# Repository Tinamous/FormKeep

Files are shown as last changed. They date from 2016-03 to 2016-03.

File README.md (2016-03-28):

Form Keep
=========

A UV exposure box and Tray store (to keep your trays in) for the Form 1, 1+ and 2 printers.

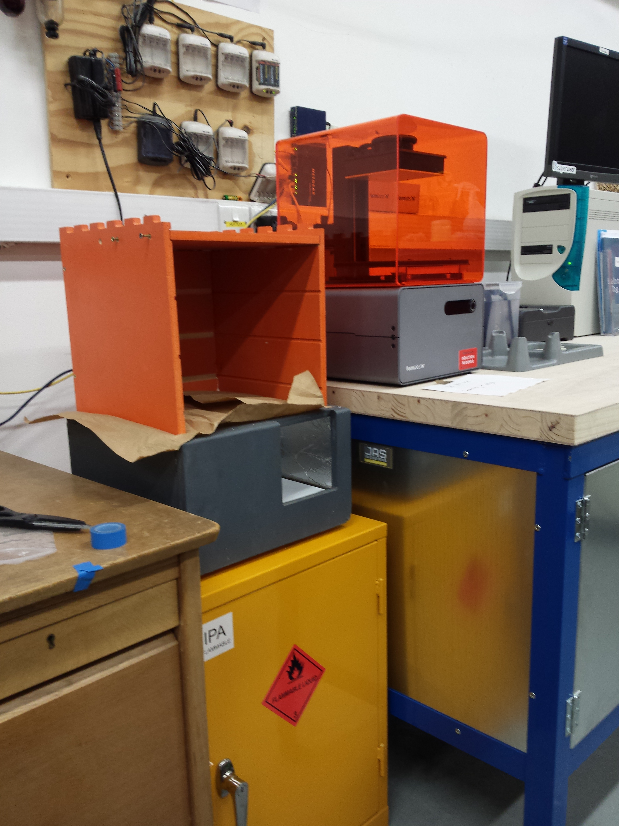
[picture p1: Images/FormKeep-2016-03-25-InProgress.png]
Form Keep UV box and tray storage


Features:
* UV exposure in base unit on 30 minute timer with countdown "clock" style neopixel display on front door.
* 3x shelfs for tray storage.
* 1x top open shelf for sand paper storage
* 1x small (25mm) area under lowest shelf for possible other storage
* Door sensors for top unit to tell if the door is open, and hence light getting to trays
* Ventilation in the base unit to prevent a build up of IPA vapours in the box
* White LEDs in base unit to allow the part to be seen clearly when the door is open

Construction:
* Top and bottom units are made of 12mm MDF (2 sheets 600x1200mm)
* Door on base made from 18mm MDF
* Feet made from 12mm MDF glued to base, then adjustable feet set into that
* Door for top unit made with 3mm acrylic
* Shelfs made with 5mm acrylic, colour to match the resin
* Front door panel 3mm clear acrylic
** 3D printed support for 12 pixel NeoPixel ring for count down timer
* Fan panel made with 3mm acrylic (ideally a scrap piece as it's not seen)
* Fan is 80mm PC fan (with yellow pulse wire ignored)
* Base panel 3mm acrylic. Can be any color
* Inside is coated with tin foil (glued to the MDF) to help reflect the UV rays

Cut using CNC router, can be hand cut if no CNC available using the svg files as cutting plans.

Roundovers done by hand router as it's quicker. 
* Bottom of the base unit has large round over on each side coming out thought the door but not along door.
* Top of base unit has small round over on sides and front of door.

Painting:
* Base unit grey (The grey in the picture is actually just undercoat which works well).
* Top unit orange

Electronics:
* Uses V2.00 Kitchen Lights Controller from https://github.com/Tinamous/KitchenLightsController
* Channel 1 & 2 used to drive UV LEDs. 
* 2x 5M strips of UV LEDs, split into 900mm lengths (to make it easier to fit), each individually wired back to the PCB.
* 2x 300mm White LEDs connected to channel 3
* 1x PC fan connected to channel 4 with protection diode across either the terminal block or headers (depending on which is free).
* USB power controller not fitted to board.
* Max 0.05R current sense resistor (5-10A load due to UV LEDs).
* Hall effect transistor used for door sensor (rather than have switch in possible explosive environment of IPA vapours).
** Connected to Button input on PCB
* Hall effect sensor to top unit door on PIR input
* TEMT6000 breakout board for light level sensor on top unit connected to Light Sensor on PCB
* Optional temperature sensors in base and top units connected to temperature sensor input
* Optional buzzer wired on breakout area of PCB.
* 12 pixel NeoPixel ring. 12th (last) pixel should be at 12 O'Clock position
** https://www.adafruit.com/products/1643
* Use 5V switching regulator rather than 7805 due to NeoPixel load (see eBay), or fit good heatsink to 7805. (360mA max load from NeoPixels, + 100mA from Photon).
* Needs a good 5-10A 12V DC power supply.
* Use Particle Photon to drive, connect to Tinamous.com to allow remote monitoring of light, temperature and more inportantly time remaining.

Bugs
----

* Back Panel slots are out of alignment with side panel slots on top unit.
* Top unit slots are to shallow (3mm, with 1mm error on Z alignment due to MDF varience and 1mm allowance for tollerance on the acrylic shelfs this leaves a potential 1mm overlap on one side.
* Front foor, opening is far to big (much bigger than Form2 display).
* Ribon cable pocket is not deep enough on base.
* Top shelf currently split in 2 which is not ideal for stopping the light get into the top resin tray. Needs an extra sheet.

Timing: See http://formlabs.com/support/finishing/post-curing-prints/

[MainPicture]: https://github.com/Tinamous/FormKeep/raw/master/Images/FormKeep-2016-03-25-InProgress.png "Form Keep UV box and tray storage - In Progress"

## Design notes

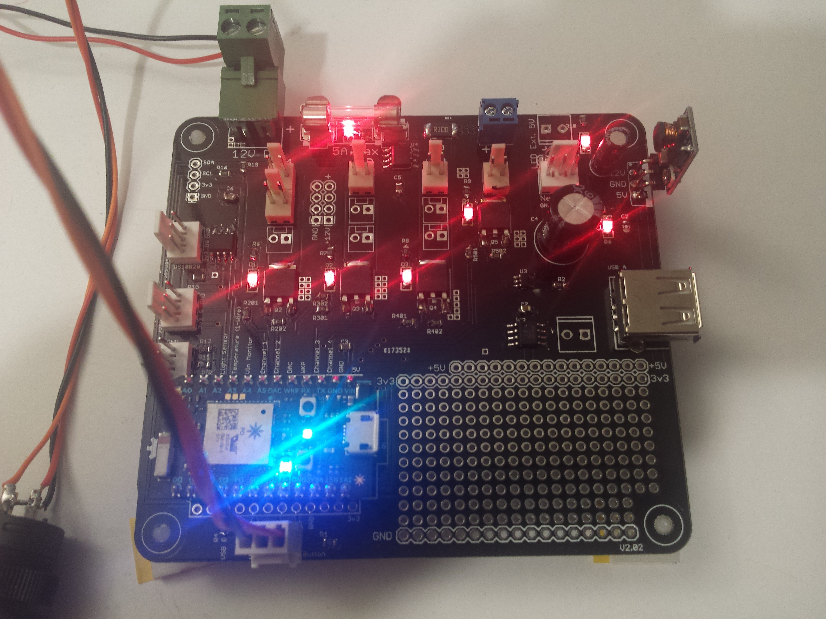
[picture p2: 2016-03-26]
Images/FormKeep-2016-03-20-PCB.png

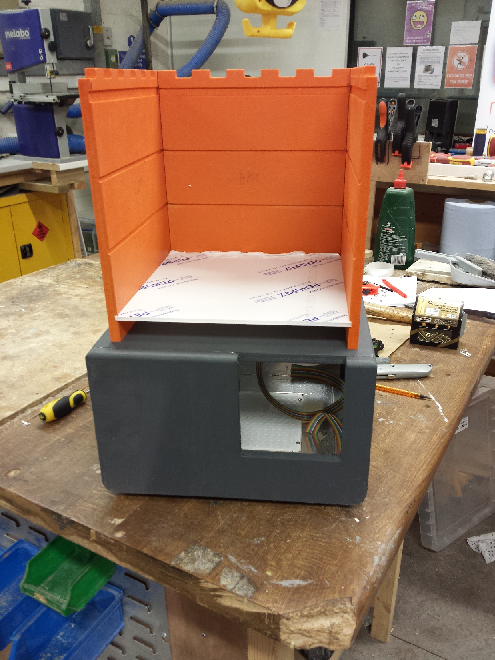
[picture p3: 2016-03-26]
Images/FormKeep-2016-03-25-WithShelf.png

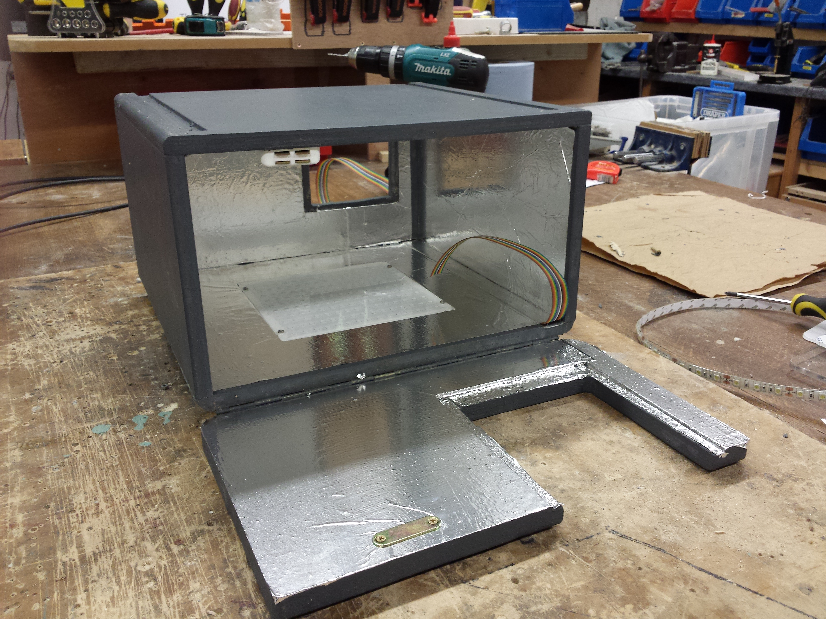
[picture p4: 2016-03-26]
Images/FormKeep-2016-03-25-InsideBase.png

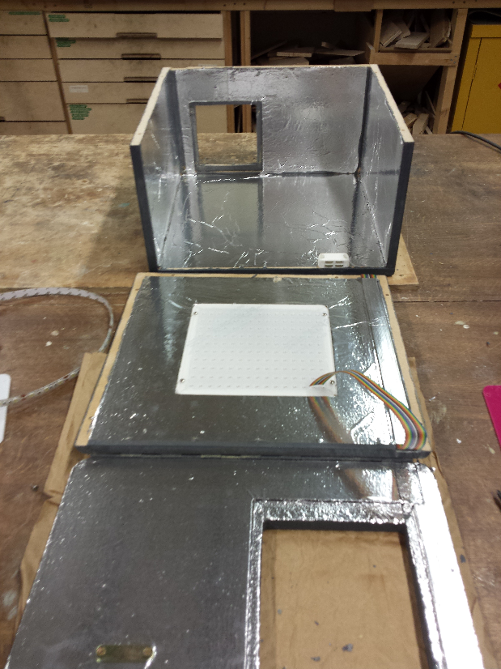
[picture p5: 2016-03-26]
Images/FormKeep-2016-03-25-InsideBaseOpen.png

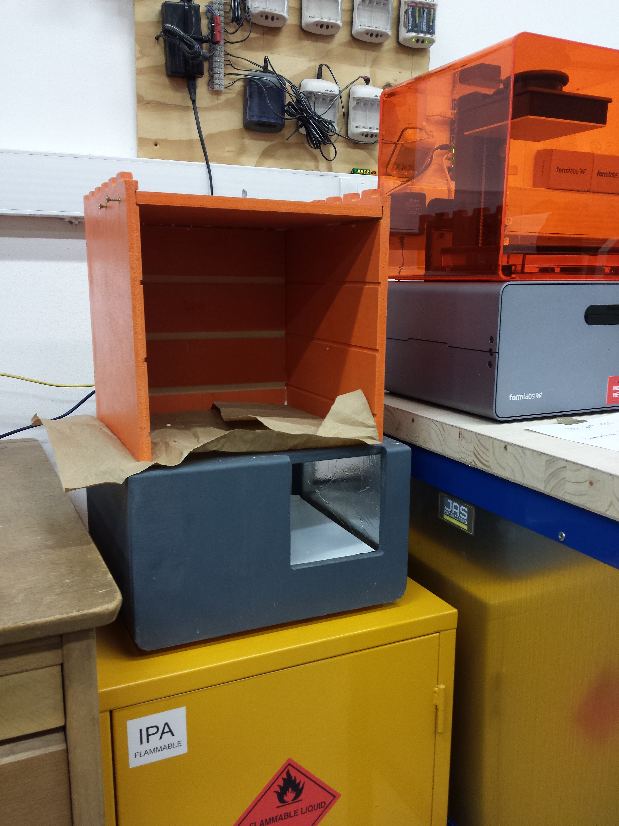
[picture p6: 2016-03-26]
Images/FormKeep-2016-03-25-InProgress-2.png

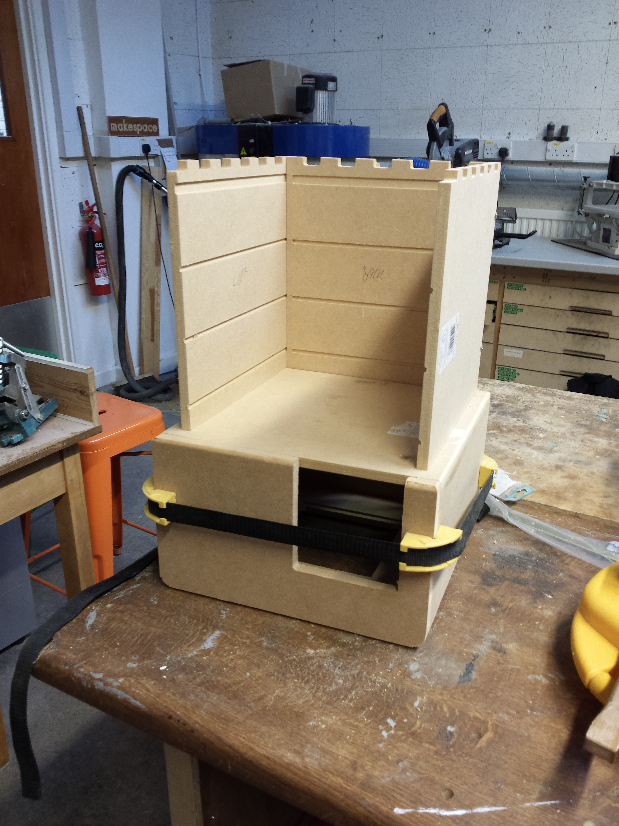
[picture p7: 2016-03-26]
Images/FormKeep-2016-03-22-BeforePaint.png

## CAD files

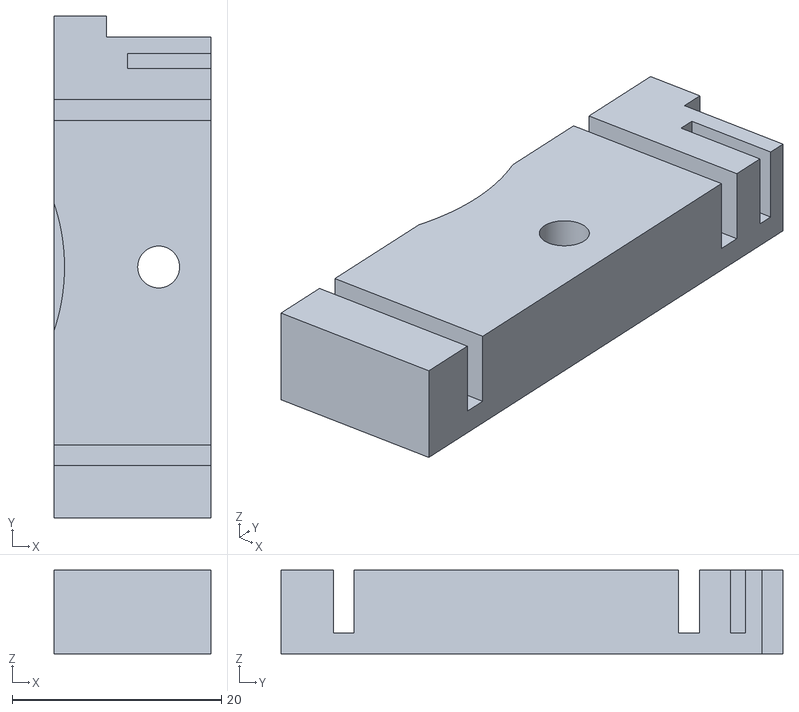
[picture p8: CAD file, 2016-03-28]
3D Printed/FrontPanelSupport.stl
15.0 x 48.0 x 8.00

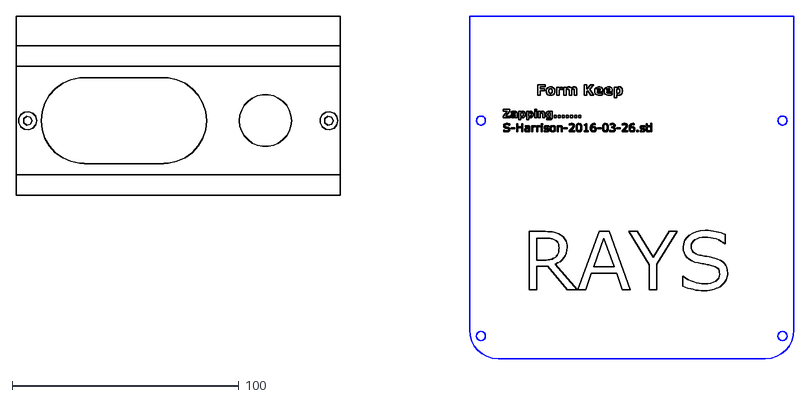
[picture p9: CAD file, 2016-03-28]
Acrylic/FormKeep-FrontPanel-Acrylic-3mm-Clear-With3DPrintedThing.dxf
343.0 x 151.0

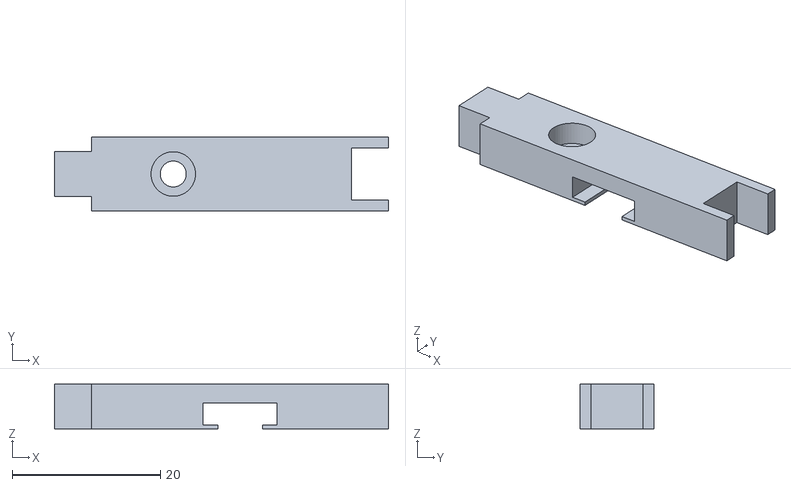
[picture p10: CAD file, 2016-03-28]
3D Printed/LedStripHolder-Single.stl
45.0 x 10.0 x 6.00

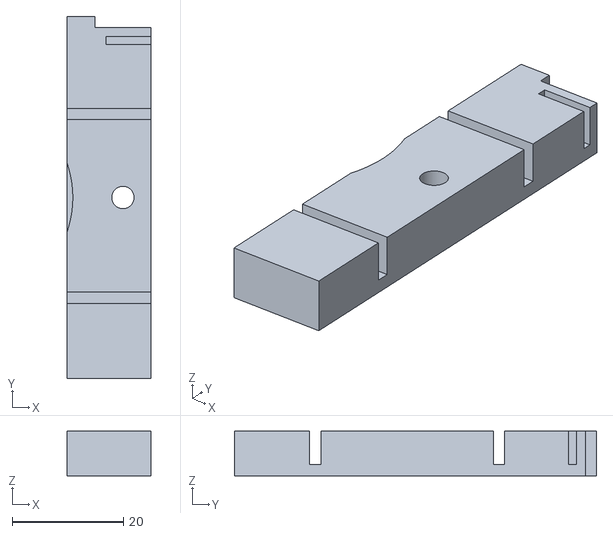
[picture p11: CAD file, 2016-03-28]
3D Printed/FrontPanelSupport-High.stl
15.0 x 65.0 x 8.00

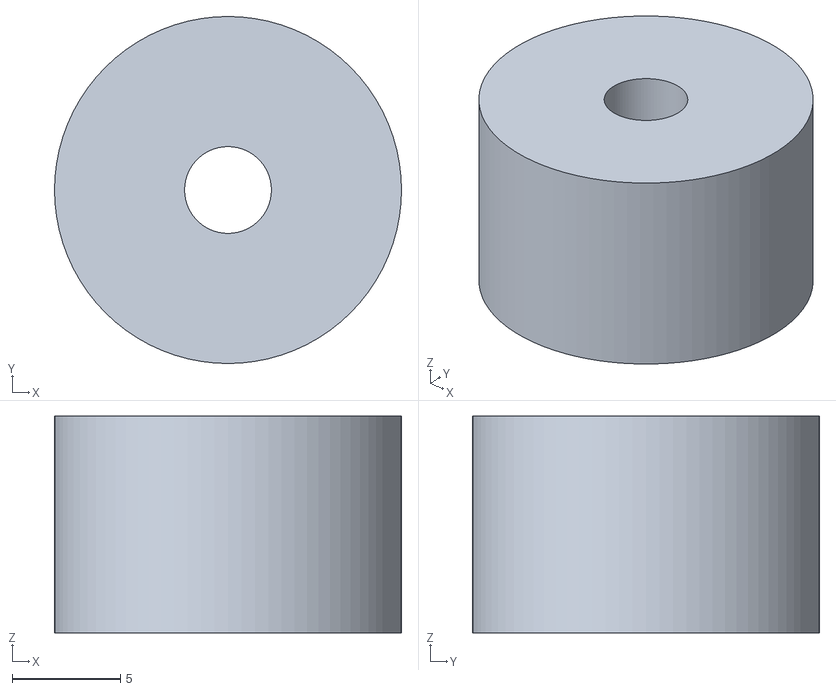
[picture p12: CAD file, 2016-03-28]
3D Printed/PcbStandoffs.stl
16.0 x 16.0 x 10.0

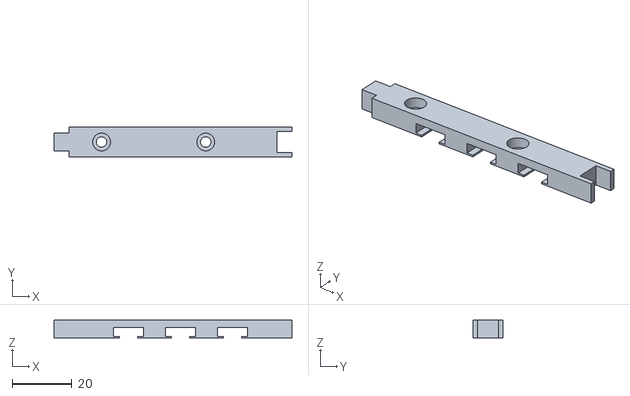
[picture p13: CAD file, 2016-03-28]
3D Printed/LedStripHolder-DoubleWidth-TrippleHolder.stl
80.0 x 10.0 x 6.00

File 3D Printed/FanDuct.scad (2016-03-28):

width = 80;
distanceBetweenHoles = 72; //
fanDuctDiameter = 74;
$fn = 128;

holeOffset = (width-distanceBetweenHoles) / 2;

module basePlate() {
    difference() {
        union() {
            cube([width,width,2]);
        }
        union() {
            translate([width/2, width/2,0]) {
                cylinder(d=fanDuctDiameter, h=2);
            }
        }
    }
}

module fanScrewHoles() {
    translate([holeOffset,holeOffset,0]) {
        cylinder(d=4, h=3);
    }

    translate([width -holeOffset,holeOffset,0]) {
        cylinder(d=4, h=3);
    }

    translate([holeOffset,width-holeOffset,0]) {
        cylinder(d=4, h=3);
    }

    translate([width -holeOffset, width - holeOffset,0]) {
        cylinder(d=4, h=3);
    }
}

ductHeight = 100;
ductDepth = 50;

module hollowCube() {
    translate([0,0,5]) {
        rotate([12,0,0]) {
            difference() {
                union() {
                    translate([(width-fanDuctDiameter+8)/2, 6, 0]) {
                        cube([fanDuctDiameter-8, ductHeight, ductDepth]);
                    }
                }
                union() {
                    translate([(width-fanDuctDiameter+8)/2+4, 6+4, 0]) {
                        cube([fanDuctDiameter-8-8, ductHeight+8, ductDepth-2]);
                    }
                }
            }
        }
    }
}


difference() {
    union() {
        basePlate();
        // Hull section between basePlate and hollow cube.
        hollowCube();
    }
    union() {
        fanScrewHoles();
    }
}

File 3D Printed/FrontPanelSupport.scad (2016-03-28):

$fn = 200;

// Ideal panel width was 115mm
// but cut was outside marking
// so is actually 143mm wide with 9mm overlap.
// If you cut yours correctly reduce this.
// Excludes possible fixing to wooden door.
PanelWidth = 143; // mm Actylic panel only. 

// Offset from left/right side for the mounting holes on the panel
MountingHolesOffset = 5;

// Height of the Acrylic panel
// need to exclude top 12-15mm for unit overlap. 
// Botton has rounded corners.
PanelHeight = 151; // mm

NeoPixelRingOuterDiameter = 38; // mm
NeoPixelRingInnerDiameter = 23; // mm

Height = NeoPixelRingOuterDiameter + 10 + 17; // 5mm top/bottom.
Depth = 8; // mm

NeoPixelXPosition = 110; 
NeoPixelYPosition = Height / 2; //24mm from the top. // Height / 2;
NeoPixelHeight = 4.5; // mm - includes wires (& probably hotmelt)

module frontPanelInsert() {
    difference() {
        union() {
            cube([PanelWidth, Height, Depth]);
        }
        union() {
            // Mounting holes
            translate([MountingHolesOffset, Height/2, 0]) {
                cylinder(d=4, h=Depth, centre=true);
                cylinder(d=8, h=3, centre=true);
            }
            translate([PanelWidth-MountingHolesOffset, Height/2, 0]) {
                cylinder(d=4, h=Depth, centre=true);
                cylinder(d=8, h=3, centre=true);
            }
           
            
            // Hole through the block for light to come through the center of the NeoPixel Display
            translate([NeoPixelXPosition, NeoPixelYPosition, 0]) {
                cylinder(d=NeoPixelRingInnerDiameter, h=Depth, centre=true);
                
                translate([0,0, Depth-NeoPixelHeight]) {
                    cylinder(d=NeoPixelRingOuterDiameter, h=NeoPixelHeight, centre=true);
                }
            }
            
            // Pocket for NeoPixel ring to sit in.
            
            // Channels for wires to escape from NeoPixels.
            // 2mm from top, exit to the right of the neo pixels
            translate([NeoPixelXPosition, NeoPixelYPosition + (NeoPixelRingOuterDiameter/2)-2-3, 2]) { 
                // Din/DOut wires.
                cube([PanelWidth - NeoPixelXPosition, 2, Depth-2]);
            }
            
            translate([NeoPixelXPosition, NeoPixelYPosition - (NeoPixelRingOuterDiameter/2), 2]) { 
                // +Ve and GND
                cube([PanelWidth - NeoPixelXPosition, 2, Depth-2]);
            }
            
            // Oval cutout to look like Form1.
            translate([30, NeoPixelYPosition, 0]) {
                cylinder(d=NeoPixelRingOuterDiameter, h=Depth, centre=true);
                
                translate([0,-(NeoPixelRingOuterDiameter/2), 0]) {
                    cube([35 ,NeoPixelRingOuterDiameter,Depth]);
                }
                
                translate([35,0, 0]) {
                    cylinder(d=NeoPixelRingOuterDiameter, h=Depth, centre=true);
                }
            }
            
            // cut out for Hall Effect door sensor.
            magnetHeightAllowance = 2; // mm
            translate([PanelWidth-10, Height-magnetHeightAllowance, 0]) {
                // Cut out all the way trough to allow for the magnet offset from 
                // the lid of the unit.
                #cube([10, magnetHeightAllowance, 10]);
                
                // Make a pocket for the hall effect device.
                // Move in slightly to allow for x-axis error on magnet alignment.
                // Move down slightly to allow for a wall on the panel
                // Move up down so as to not cut all the way through the panel.
                // and mount it at the back of the panel
                translate([2, -3, 2]) {
                    // Hall effect is about 1.6mm deep
                    #cube([10, 1.5, Depth-2]);
                }
            }
            
            // DEGUB!
            // Chop out most of the panel to get just the hall effect section
            // in order to test print
            cube([PanelWidth-15, Height, Depth]);
        }
    }
}

frontPanelInsert();

// For SVG explort

projection( cut=false ) {
//    frontPanelInsert();
}

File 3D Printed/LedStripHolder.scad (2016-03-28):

// Max height 270mm.
// Make 200mm height so 70mm bottom of box for raised
// area that will allow solvent to drain from part.
MaxHeight = 250;
MaxHeight = 70;
//MaxHeight = 35;

blockSize = 35; // 35mm (excludes key slot).

blockKeyWidth = 6;

blockDepth = 6;

// 1 == Single
// 2 == Double with middle strip.
blockType = 2;

$fn=50;

module ledGrip() {
    
                
    // LED strip holes
    translate([0,0,0.5]) {
        cube([10,10,3]);
    }

    // 2mm offset either side to keep hold of the LED.
    translate([2,0,0]) {
        cube([6,10,0.5]);
    }
}

// If multiple blocks use zero tollerance
// includeMiddleStripHolder - if holder for LED strip in the middle of the two main ones.
// i.e. for white LED strip between the two UV strips.
module block(blockCount, blockConnectTollerance, includeMiddleStripHolder) {

length = (blockCount * blockSize) + 5 ;

    difference() {
        union() {
            translate([0,2,0]) {
                cube ([length,blockKeyWidth,blockDepth]);
            }
            
            // Move down 10mm
            // Add outer blocks either side
            // to connect one segment to the next.
            translate([5,8,0]) {
                cube([length,2,blockDepth]);
            }
            
            translate([5,0,0]) {
                cube([length,2,blockDepth]);
            }
        }
        union() {
            
            for (offset = [16 : 35 : length]) {
            
                // Mounting holes
                translate([offset,5,0]) {
                    cylinder(d=3.5,h=blockDepth);
                    
                    // Large hole for head of screw
                    translate([0,0,3]) { 
                        cylinder(d=6,h=blockDepth-3);
                    }
                    
                }
            }
            
            // Holes to hold the LED strip in place.
            for (offset = [20 : 35 : length-10]) {
                translate([offset,0,0.0]) {
                    ledGrip();
                }
            }
            
            // for double strips, insert a middle
            //  
            if (includeMiddleStripHolder) {
                for (offset = [37.5 : 70 : length]) {
                    translate([offset,0,0.0]) {
                        ledGrip();
                    }
                }
            }
            
            // cut out a tiny bit extra from the open end to 
            // allow for variance in printing
            // Offset is 2mm either wide.
            translate([length,2 - blockConnectTollerance,0]) {
                // Allow 0.5mm spacing for key to fit.
                cube ([5,blockKeyWidth + (2* blockConnectTollerance),blockDepth]);
            }
        }
    }
}

//block(2, 0.5, true);
//block(2, 0.5, false);

if (blockType == 1) {
    block(1, 0.5, false);
} else if (blockType == 2) {
    block(2, 0.5, true);
}

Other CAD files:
3D Printed/PcbStandoffs.scad

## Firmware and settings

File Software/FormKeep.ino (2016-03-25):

// This #include statement was automatically added by the Particle IDE.
#include "IdleState.h"

// This #include statement was automatically added by the Particle IDE.
#include "TimerRunningState.h"

// This #include statement was automatically added by the Particle IDE.
#include "adafruit-ina219/adafruit-ina219.h"

// This #include statement was automatically added by the Particle IDE.
#include "neopixel/neopixel.h"

// This #include statement was automatically added by the Particle IDE.
#include "OneWire/OneWire.h"

//////////////////////////////////////////////////////////////////////////
// FORM [1/1+/2] KEEP. UV box control + monitoring.
//////////////////////////////////////////////////////////////////////////
// V2.02  board
//////////////////////////////////////////////////////////////////////////
int BoardVersion = 3;

// D0/D1 - I2C only

// USV String 1
int uvString1Pin = A4; // Channel 1
int uvString2Pin = A5; // Channel 2
int whiteLedsPin = RX; // Channel 3
int fanPin = TX; // Channel 4

// User panel switch
// Door sensor hall effect switch input
int switchPin = D6;
// Door sensor hall effect Power.
int switchDrivePin = D7;

int vInPin = A3;
OneWire ds = OneWire(A2);  // 1-wire signal on pin D4
int lightLevelPin = A1;
int pirPin = A0;



// byte sensor1[] = {0x28, 0xD6, 0xA9, 0x4E, 0x07, 0x00, 0x00, 0x27};
// onboard temperature sensor address.
// TODO: Allow for UV box temperature, Upper box temperature and external temperature.
byte sensor[8];

// Current sensor
Adafruit_INA219 ina219;

//////////////////////////////////////////////////////////////////////////
// Particle Functions
//////////////////////////////////////////////////////////////////////////
int on(String command);
int off(String command);
int startTimer(String command);
int stopTimer(String args);
int setTimer(String args);

//////////////////////////////////////////////////////////////////////////
// State
//////////////////////////////////////////////////////////////////////////
// State:
// 0: Idel
// 1: timer running
// 10: timer complete, waiting for user to remove the itme
int currentState = 0;

//////////////////////////////////////////////////////////////////////////
// Interrup flags
//////////////////////////////////////////////////////////////////////////
volatile bool doorOpened = false;
volatile bool trayDoorOpened = false;


// Setup NeoPixel (clock) circle.
#define PIXEL_PIN D5
#define PIXEL_COUNT 12
#define PIXEL_TYPE WS2812B

Adafruit_NeoPixel strip = Adafruit_NeoPixel(PIXEL_COUNT, PIXEL_PIN, PIXEL_TYPE);

// Monitoring variables
float temperatureCelsius = 0;
double currentMilliAmps = 0;
double voltsIn = 0; // 5V rail monitor.
double supplyVoltage = 0; // the 12V in (monitored via current sensor)

// How many seconds to wait before turning off the lights.
double lightsOffInSeconds = 0;

// Measurement timer. Every n seconds.
Timer countDownTimer(1000, countDownTimerTick);

void setup() {
    
    // Setup NeoPixel LED (strip).
    strip.begin();
    strip.show(); // Initialize all pixels to 'off'
    
    // Smile.
    for (int i=2; i<=8; i++ ) {
        strip.setColorDimmed(i, 0, 255, 0, 128);
    }
    strip.setColorDimmed(0, 0, 0, 255, 128);
    strip.setColorDimmed(10, 0, 0, 255, 128);
    strip.show();
    
    // Power drives.
    pinMode(uvString1Pin, OUTPUT);
    pinMode(uvString2Pin, OUTPUT);
    pinMode(whiteLedsPin, OUTPUT);
    pinMode(fanPin, OUTPUT);
    
    // Switch
    pinMode(switchPin, INPUT_PULLUP); // Interrupt.
    pinMode(switchDrivePin, OUTPUT);
    
    // Sensors
    pinMode(vInPin, INPUT);
    pinMode(lightLevelPin, INPUT);
    // PIR input must be reduced to guard against 5v.
    pinMode(pirPin, INPUT); // Hall effect #2 on upper case
    
     
    digitalWrite(uvString1Pin, false);
    digitalWrite(uvString2Pin, false);
    digitalWrite(whiteLedsPin, false);
    digitalWrite(fanPin, false);
    digitalWrite(switchDrivePin, true);
     
    Particle.function("startTimer", startTimer);
    Particle.function("stopTimer", stopTimer);
    Particle.function("on", on); // Args: "Fan", "UV", "White"
    Particle.function("off", off);// Args: "Fan", "UV", "White"
    Particle.function("setTimer", setTimer); // Args: time in seconds for the standard timer.
    
    // Initialize the INA219.
    // By default the initialization will use the largest range (32V, 2A).  However
    // you can call a setCalibration function to change this range (see comments).
    // NB: Check which resistor is to be used. Probably 0R05 due to high current.
    ina219.begin();

    // interrupt on the falling edge of A7 (switch pulled low)
    attachInterrupt(switchPin, doorOpenedIsr, FALLING);
    
    // attachInterrup to PIR (Hall effect #2) pin
    attachInterrupt(pirPin, upperDoorOpenedIsr, RISING);
    
    listTemperatureSensors();

    Particle.publish("Status", "Form Keep. Version: 0.2.1.");
    Particle.publish("Version", "0.2.1");
    
    
    //countDownTimer.start();
}

int loopCounter = 0;
// the last value of lightsOffInSeconds that was used for setting the clock.
int lastLightsOffInSeconds = 0;
bool doorOpen = false;
bool trayDoorOpen = false;
bool uvLedsOn = false;
bool whiteLedsOn = false;
bool fanOn = false;

void loop() {
    if (currentState == 1 && lightsOffInSeconds <=0) {
        stopUVTimer();
    }
    
    loopCounter++;
    if (loopCounter > 200) {
        loopCounter = 0;
        //takeMeasurements();
    }
    
    if (doorOpened) {
        Particle.publish("Status", "Door opened.", 60, PRIVATE);
        
        // If currently idle waiting for blah...
        if (currentState == 0) {
            // Immediatly start the fan to keep IPA vapours low
            switchFanOn();
            switchWhiteLedsOn();
            waitForDoorClose();
            startUVTimer();
        }
        
        // If currently running UV Timer
        if (currentState == 1) {
            // leave lights on.
            // Don't switch the lights on when opened during UV exposure.
            // switchWhiteLedsOn();
        }
        
        // Finished waiting for user to open door.
        if (currentState == 10) {
            Particle.publish("Status", "State = 10, moving to state 0", 60, PRIVATE);
            // user is taking thing out.
            waitForDoorClose();
            switchWhiteLedsOff();
            // restore state to idle.
            currentState = 0;
        }
        
        // Debouce.
        delay(500);
        doorOpened = false;
    }
    
    // if the tray door was opened and it is not already open
    if (trayDoorOpened) {
        Particle.publish("Status", "Tray door opened.", 60, PRIVATE);
        trayDoorOpen = true;
        trayDoorOpened = false;
    }
    
    if (trayDoorOpen) {
        // Check to see if it has now been closed.
        // if so, we can set trayDoorOpen to false.
        // If it's been open for some time we
        // need to beep......
    }
    
    if (lightsOffInSeconds != lastLightsOffInSeconds ) {
        lastLightsOffInSeconds = lightsOffInSeconds;
        
        // Update Neopixel clock.
        for (int i=0; i<12; i++) {
            // uint16_t aLedNumber, byte aRed, byte aGreen, byte aBlue, byte aBrightness
            if (lightsOffInSeconds > ((11-i) * 10)) { // each pixel worth 10 seconds
                strip.setColorDimmed(i, 0, 255, 255, 128);
            } else {
                strip.setColorDimmed(i, 0, 0, 0, 0);
            }
        }
        strip.show();
    }
    
    if (!isDoorClosed()) {
        switchWhiteLedsOn();
    }
    
    if (whiteLedsOn && isDoorClosed()) {
        // Ensure the White LED is switched off if the door was opened but
        // is now closed.
        switchWhiteLedsOff();
    }
    
    updateFanSpeed(!isDoorClosed());
    
    delay(50);
}

void waitForDoorClose() {
    // TODO: Read switch input until or high...

    // switchPin is LOW when door is open.
    while (!digitalRead(switchPin)) {
        delay(10);
    }
    //Particle.publish("Status", "Door closed.", 60, PRIVATE);
}

// Timer.
void countDownTimerTick() {
    lightsOffInSeconds--;   
}

void startUVTimer() {
    // TODO: Use EEPROM value
    lightsOffInSeconds = 120;
    
    switchUVOn();
    switchWhiteLedsOff();
    switchFanOn();
    currentState = 1;
    
    // Update Neopixel clock to show full time
    for (int i=0; i<12; i++) {
        strip.setColorDimmed(i, 0, 255, 0, 128);
    } 
    strip.show();
            
    countDownTimer.start();
    
    Particle.publish("Status", "Timer Started", 60, PRIVATE);
}

void stopUVTimer() {
    countDownTimer.stop();
    
    // UV Exposure finished. Now waiting for user to open door to 
    // remove their thing.
    currentState = 10;
    
    switchUVOff();
    switchFanOff();
    
    for (int i=0; i<12; i++) {
        strip.setColorDimmed(i, 0, 0, 0, 0);
    }
    strip.show();
    
    // TODO: Use EEPROM value
    if (lightsOffInSeconds = 0) {
        Particle.publish("Status", "UV Exposure Complete.", 60, PRIVATE);
    } else {
        Particle.publish("Status", "Timer Stopped", 60, PRIVATE);
    }
}

void switchUVOn() {
    if (uvLedsOn) {
        return;
    }
    Particle.publish("Status", "UV On", 60, PRIVATE);
    digitalWrite(uvString1Pin, true);
    digitalWrite(uvString2Pin, true);
    uvLedsOn = true;
}

void switchUVOff() {
    if (!uvLedsOn) {
        return;
    }
    Particle.publish("Status", "UV Off", 60, PRIVATE);
    digitalWrite(uvString1Pin, false);
    digitalWrite(uvString2Pin, false);
    uvLedsOn = false;
}

void switchWhiteLedsOn() {
    if (whiteLedsOn) {
        return;
    }
    digitalWrite(whiteLedsPin, true);
    whiteLedsOn = true;
    Particle.publish("Status", "White LEDs On", 60, PRIVATE);
}

void switchWhiteLedsOff() {
    if (!whiteLedsOn) {
        return;
    }
    digitalWrite(whiteLedsPin, false);
    whiteLedsOn = false;
    Particle.publish("Status", "White LEDs Off", 60, PRIVATE);
}

void updateFanSpeed(bool doorOpen) {
    // If the door is open, fan runs 100%.
    
    // If running 
        
    if (doorOpen) {
        if (!fanOn) {
            switchFanOn();
        }
        analogWrite(fanPin, 255, 25000);
        return;
    } 
    
    // If not currently in the timer then switch the fan off when the door is closed.
    if (currentState!=1) {
        //switchFanOff();
        return;
    } 
    
    // If within the first x of the timer, keep the fan running low.
            
    // After a preset time the vapoures should have gone
    // so we can kill the fan.
    if (lightsOffInSeconds < 10) { // 90
        switchFanOff();
        return;
    }
    
    // Otherwise run the fan slowly
    analogWrite(fanPin, 80, 25000);

}

void switchFanOn() {
    if (fanOn) {
        return;
    }
    Particle.publish("Status", "Fan On", 60, PRIVATE);
    
    // Start it fast to ensure it starts.
    analogWrite(fanPin, 255);

    //digitalWrite(fanPin, true);
    fanOn = true;
}

void switchFanOff() {
    if (!fanOn) {
        return;
    }
    Particle.publish("Status", "Fan Off", 60, PRIVATE);
    digitalWrite(fanPin, false);
    fanOn = false;
}

bool isDoorClosed() {
    // High indicates door is closed.
    return digitalRead(switchPin);   
}

// *******************************************************
// Sensor reading
// *******************************************************
void takeMeasurements() {
    if (BoardVersion >= 2) {
        // Read the temperature.
        // Show the temperature from the first sensor.
        showTemperature(sensor);
        showCurrent();
        readVin();
        
        Particle.publish("senml", "{e:[{'n':'boardTemperature','v':'" + String(temperatureCelsius) + "'},{'n':'current','v':'" + String(currentMilliAmps) + "'},{'n':'supplyVoltage','v':'" + String(supplyVoltage) + "'},{'n':'lightState','v':'" + String(currentState) + "'},{'n':'vin','v':'" + String(voltsIn) + "'}]}", 60, PRIVATE);
    }
}

void showCurrent () {
  float busvoltage = 0;
  float current_mA = 0;
  float loadvoltage = 0;

  float shuntvoltagemV = ina219.getShuntVoltage_mV();
  busvoltage = ina219.getBusVoltage_V(); // at VIN- pin.
  // Adafruit library assumes 0.1R.
  current_mA = (ina219.getCurrent_mA() * 1);
  loadvoltage = busvoltage + (shuntvoltagemV / 1000);
  
  Particle.publish("Status", "Bus: " + String(busvoltage) + "V, Supply: " + String(loadvoltage) + "V, Current: " + String(current_mA) + " mA");
  
  currentMilliAmps = current_mA;
  supplyVoltage = loadvoltage;
  
  //Serial.print("Bus Voltage:   "); Serial.print(busvoltage); Serial.println(" V");
  //Serial.print("Shunt Voltage: "); Serial.print(shuntvoltagemV); Serial.println(" mV");
  //Serial.print("Load Voltage:  "); Serial.print(loadvoltage); Serial.println(" V");
  //Serial.print("Current:       "); Serial.print(current_mA); Serial.println(" mA");
  //Serial.println("");
}

void listTemperatureSensors() {
  //Serial.println("------------------------------------------");
  //Serial.println("Sensors Discovered:");
  
  int sensorNumber = 0;
    
  do {   
    byte addr[8];
    
    if ( !ds.search(addr)) {
      ds.reset_search();
      return;
    }
  
    //Serial.print("ROM =");
    byte i;
    for( i = 0; i < 8; i++) {
      //Serial.write(' ');
      //Serial.print(addr[i], HEX);
      sensor[i] = addr[i];
    }
  
    if (OneWire::crc8(addr, 7) != addr[7]) {
        Serial.println("CRC is not valid!");
        return;
    } 
    
    // the first ROM byte indicates which chip
    switch (addr[0]) {
      case 0x10:
        Particle.publish("Status", "Found  DS18S20 ");
        break;
      case 0x28:
        Particle.publish("Status", "Found  DS18B20 :-) ");
        break;
      case 0x22:
        Particle.publish("Status", "Found  DS1822");
        break;
      default:
        Particle.publish("Status", "Found non a DS18x20 family device ");
        return;
    } 
  } while (true);
}

void showTemperature(byte sensorAddress[]) {
    byte i;
    byte present = 0;
    byte data[12];

    //  showAddress(sensorAddress); 

    // Start conversion.  
    ds.reset();
    ds.select(sensorAddress);
    ds.write(0x44);

    delay(1000);   // Delay to ensure conversion has happened. This might be update 750ms for 12bit. 375 (11 bit), 187 (10bit), 93 (9 bit)

    // Read conversion
    present = ds.reset();
    ds.select(sensorAddress);    
    ds.write(0xBE);         // Read Scratchpad
  
      // Read data
    for ( i = 0; i < 9; i++) {           // we need 9 bytes
        data[i] = ds.read();
    }
    //showData( present, data);
  
    //Serial.print(" CRC=");
    //Serial.print(OneWire::crc8(data, 8), HEX);
    //Serial.println();
  
    temperatureCelsius = computeTemperature(data);
    
    //Particle.publish("Status", "Temperature read as " + String(temperatureCelsius));

    return;
}

float computeTemperature(byte data[]) {
  // Convert the data to actual temperature
  // because the result is a 16 bit signed integer, it should
  // be stored to an "int16_t" type, which is always 16 bits
  // even when compiled on a 32 bit processor.
  int16_t raw = (data[1] << 8) | data[0];

  byte cfg = (data[4] & 0x60);
  // at lower res, the low bits are undefined, so let's zero them
  if (cfg == 0x00) raw = raw & ~7;  // 9 bit resolution, 93.75 ms
  else if (cfg == 0x20) raw = raw & ~3; // 10 bit res, 187.5 ms
  else if (cfg == 0x40) raw = raw & ~1; // 11 bit res, 375 ms
  //// default is 12 bit resolution, 750 ms conversion time
    
  float celsius;
  celsius = (float)raw / 16.0;
  return celsius;
}

void readVin() {
    int vInAdc = analogRead(vInPin);
    // convert to ADC bits to millivolts
    // then x2 as it's a potential divider.
    voltsIn = (vInAdc * 0.8 * 2);
}

// *******************************************************
// Neopixel functions
// *******************************************************
void rainbow(uint8_t wait) {
  uint16_t i, j;

  for(j=0; j<256; j++) {
    for(i=0; i<strip.numPixels(); i++) {
    //for(i=0; i<4; i++) {
      strip.setPixelColor(i, Wheel((i+j) & 255));
    }
    strip.show();
    delay(wait);
  }
}

// Input a value 0 to 255 to get a color value.
// The colours are a transition r - g - b - back to r.
uint32_t Wheel(byte WheelPos) {
  if(WheelPos < 85) {
   return strip.Color(WheelPos * 3, 255 - WheelPos * 3, 0);
  } else if(WheelPos < 170) {
   WheelPos -= 85;
   return strip.Color(255 - WheelPos * 3, 0, WheelPos * 3);
  } else {
   WheelPos -= 170;
   return strip.Color(0, WheelPos * 3, 255 - WheelPos * 3);
  }
}

// *******************************************************
// Particle function functions (i.e. Internet exposed
// *******************************************************)

// Args: "Fan", "UV", "White"
int on(String args) {
    
    if (args == "Fan") {
        switchFanOn();
        return 1;
    } else if (args == "UV") {
        switchUVOn();
        return 2;
    } else if (args == "White") {
        switchWhiteLedsOn();
        return 3;
    }
    
    return 255;
}
// Args: "Fan", "UV", "White"
int off(String args) {
    
    if (args == "Fan") {
        switchFanOff();
        return 1;
    } else if (args == "UV") {
        switchUVOff();
        return 2;
    } else if (args == "White") {
        switchWhiteLedsOn();
        return 3;
    }

    return 0;
}

int startTimer(String args) {
    Particle.publish("Status", "Starting timer");
    startUVTimer();
    return 1;
}

int stopTimer(String args) {
    Particle.publish("Status", "Stopping timer");
    stopUVTimer();
    return 1;
}

// arg should be timer time.
int setTimer(String args) {
    Particle.publish("Status", "Setting timer time to: ...");
    
    return 0;
}

// *******************************************************
// Helpers
// *******************************************************


// *******************************************************
// Interrup service routines.
// *******************************************************
void doorOpenedIsr() {
    doorOpened = true;
}

// ISR for PIR sensor.
void upperDoorOpenedIsr() {
    trayDoorOpened = true;
}

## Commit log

2016-03-26 Added 3D designs for front panel LED
    [FrontPanelSupport-High.stl, FrontPanelSupport.scad, FrontPanelSupport.stl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]
2016-03-26 Added comments about cut out for hinge and ribon cable.
2016-03-28 Added 3D printed parts for the front panel NeoPixel support and Hall sensor holder, The LED strip holders.
    Updated alternative front panel with name and details on, included flat versions of the 3D printed support to ensure opening lines up.
    Updated readme to include timing details.
    [FanDuct.scad, FormKeep-FrontPanel-Acrylic-3mm-Clear-With3DPrintedThing.dxf, FrontPanelSupport-High.stl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]
